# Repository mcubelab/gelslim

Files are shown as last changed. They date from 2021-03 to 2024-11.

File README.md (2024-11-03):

# GelSlim 3.0
**Note:** The MCube Lab at MIT has closed and no longer distributes pre-made sensors by mail upon request.
Consider the latest version [GelSlim 4.0](https://www.mmintlab.com/research/gelslim-4-0/) at the University of Michigan's [MMint Lab](https://www.mmintlab.com/) for an easier to reproduce version of the sensor.

## Quick-Start
Please follow the [Hardware Quick Start Guide](https://github.com/mcubelab/gelslim/blob/main/Hardware/GelSlim%20Quick%20Start%20Tutorial-Updated.pdf) instructions to build your own sensor. The step-by-step resources found below are in the process of being updated.

## Step-by-Step Instructions
**Click on the pictures below for more information**

| 3-D Printing  | PCB Fabrication | Elastomer Fabrication | Assembly |
|---|---|---|---|
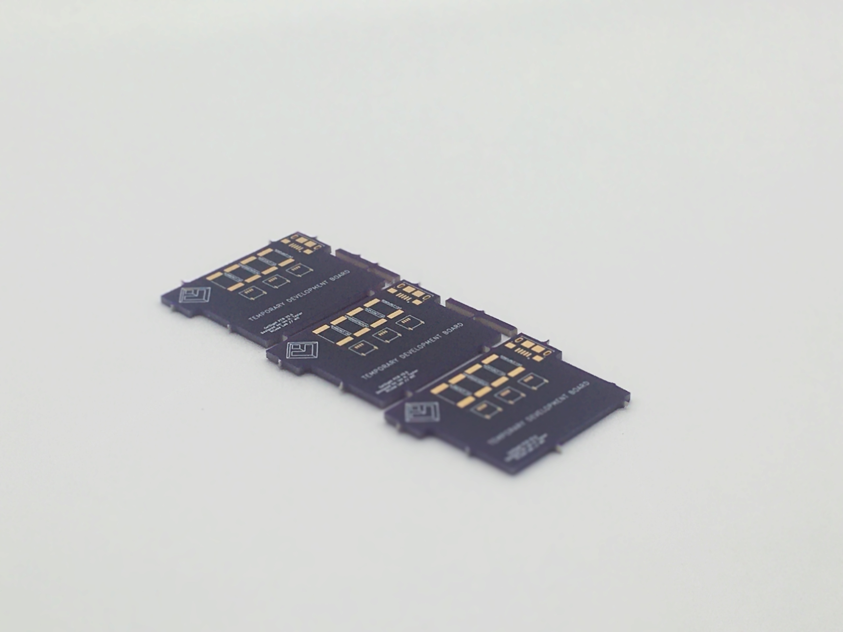
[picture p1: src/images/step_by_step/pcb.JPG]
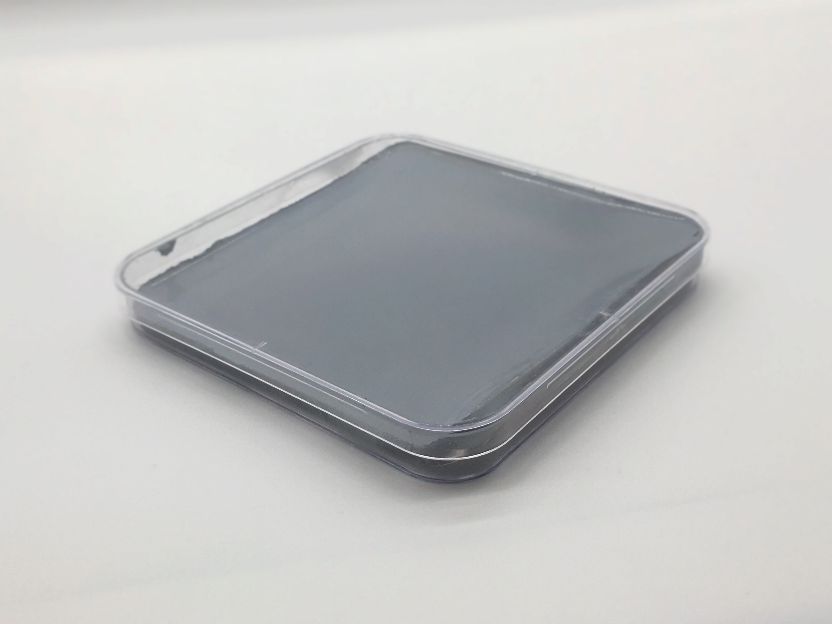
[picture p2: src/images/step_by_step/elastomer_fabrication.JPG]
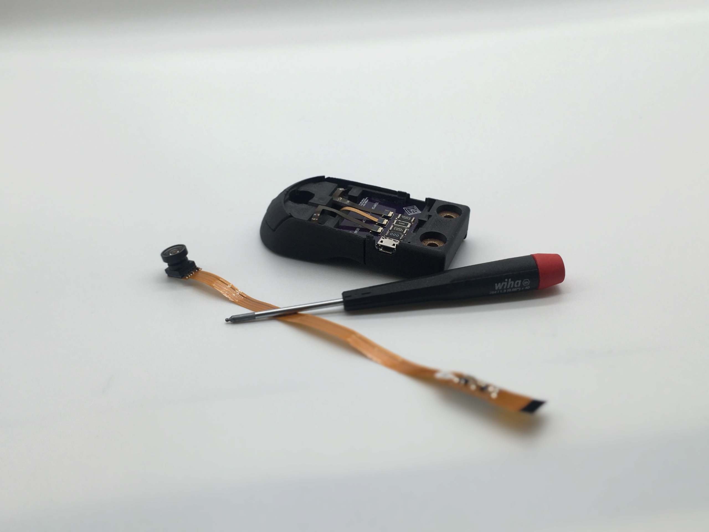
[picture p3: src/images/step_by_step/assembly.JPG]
| | | | | 

## Mechanical
| Elastomer | Fasteners | Body | Shaping Lens |
|---|---|---|---|
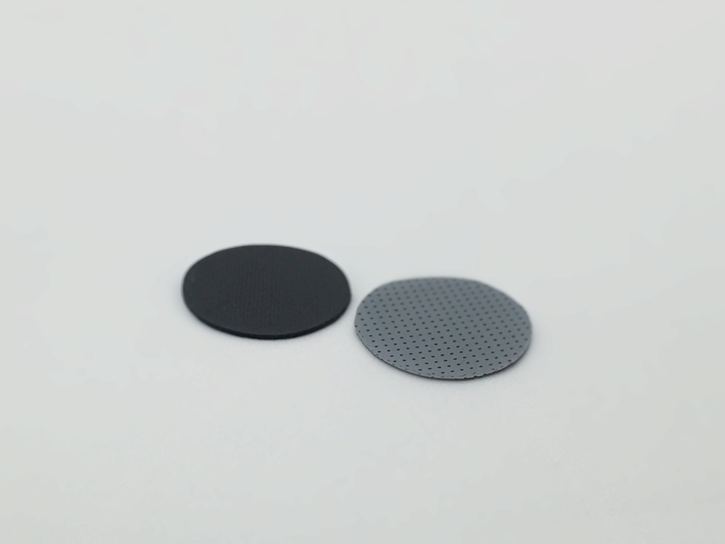
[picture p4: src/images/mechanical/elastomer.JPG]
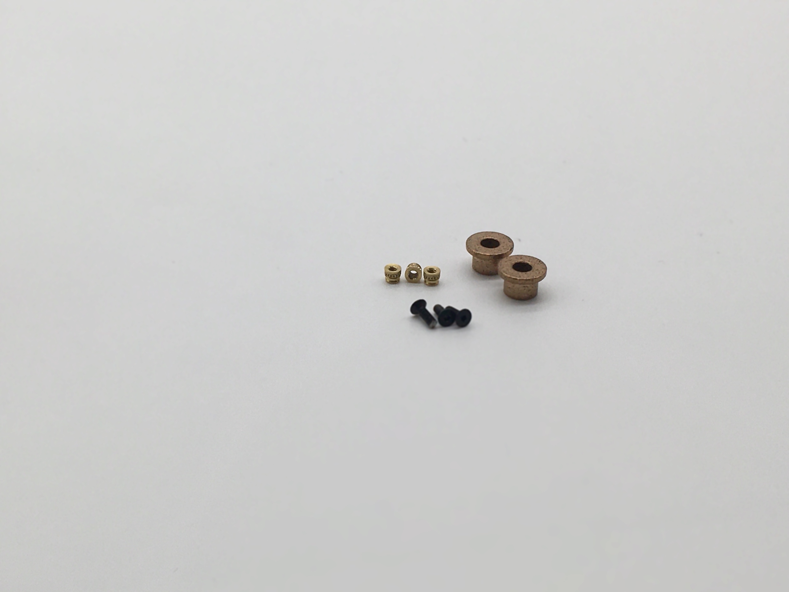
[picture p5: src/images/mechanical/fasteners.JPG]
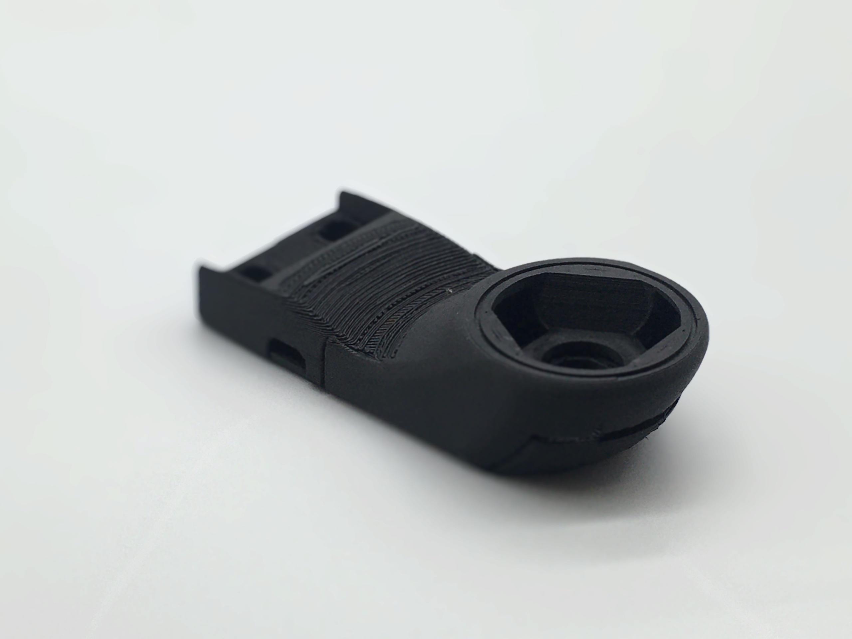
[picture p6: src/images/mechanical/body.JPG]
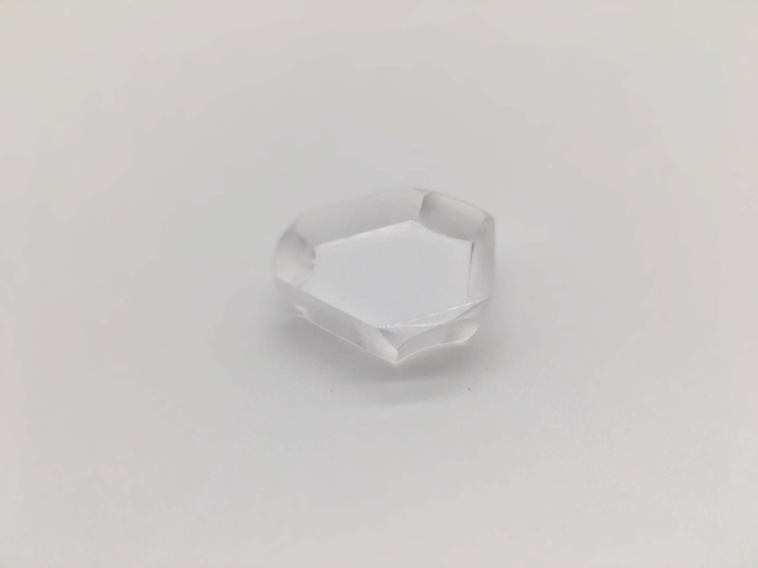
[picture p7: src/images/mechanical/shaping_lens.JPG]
| | | | | 

## Electrical
| LED Driver | LED Harness | Camera | Connectors and Adapters |
|---|---|---|---|
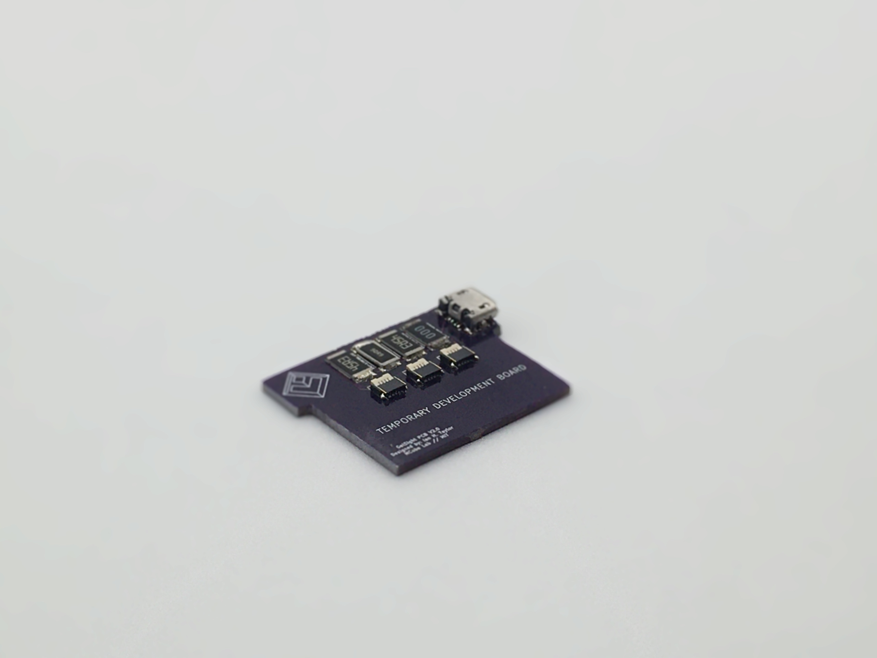
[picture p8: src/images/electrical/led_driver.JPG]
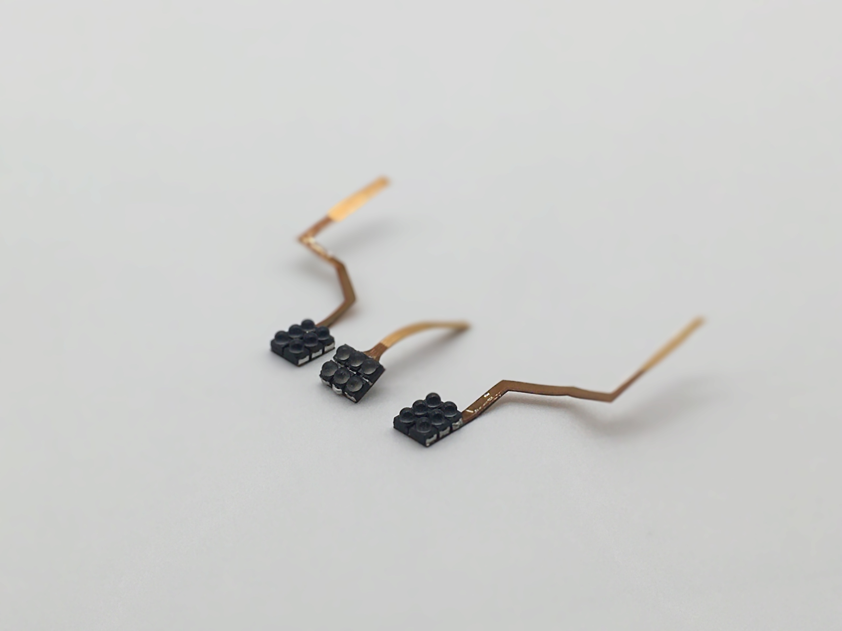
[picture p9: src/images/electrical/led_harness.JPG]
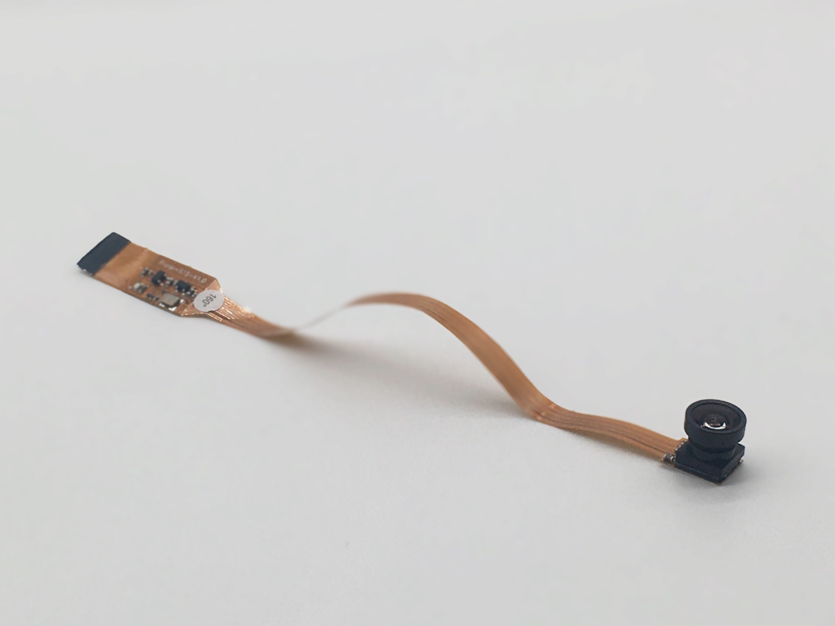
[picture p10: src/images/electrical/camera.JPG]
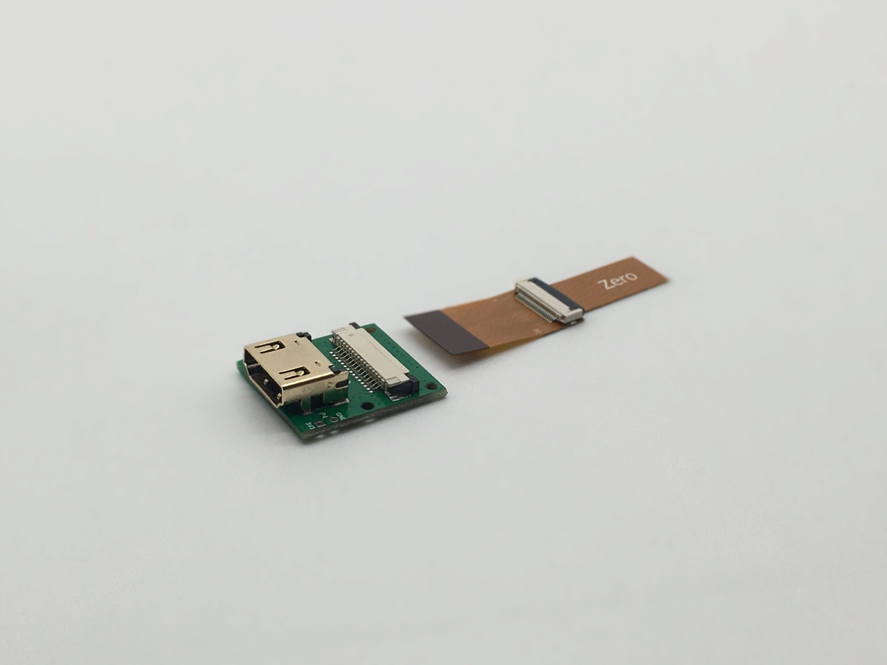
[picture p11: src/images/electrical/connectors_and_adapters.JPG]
| | | | | 

## Software
| Raspberry Pi | Dependencies | GUI | Calibration |
|---|---|---|---|
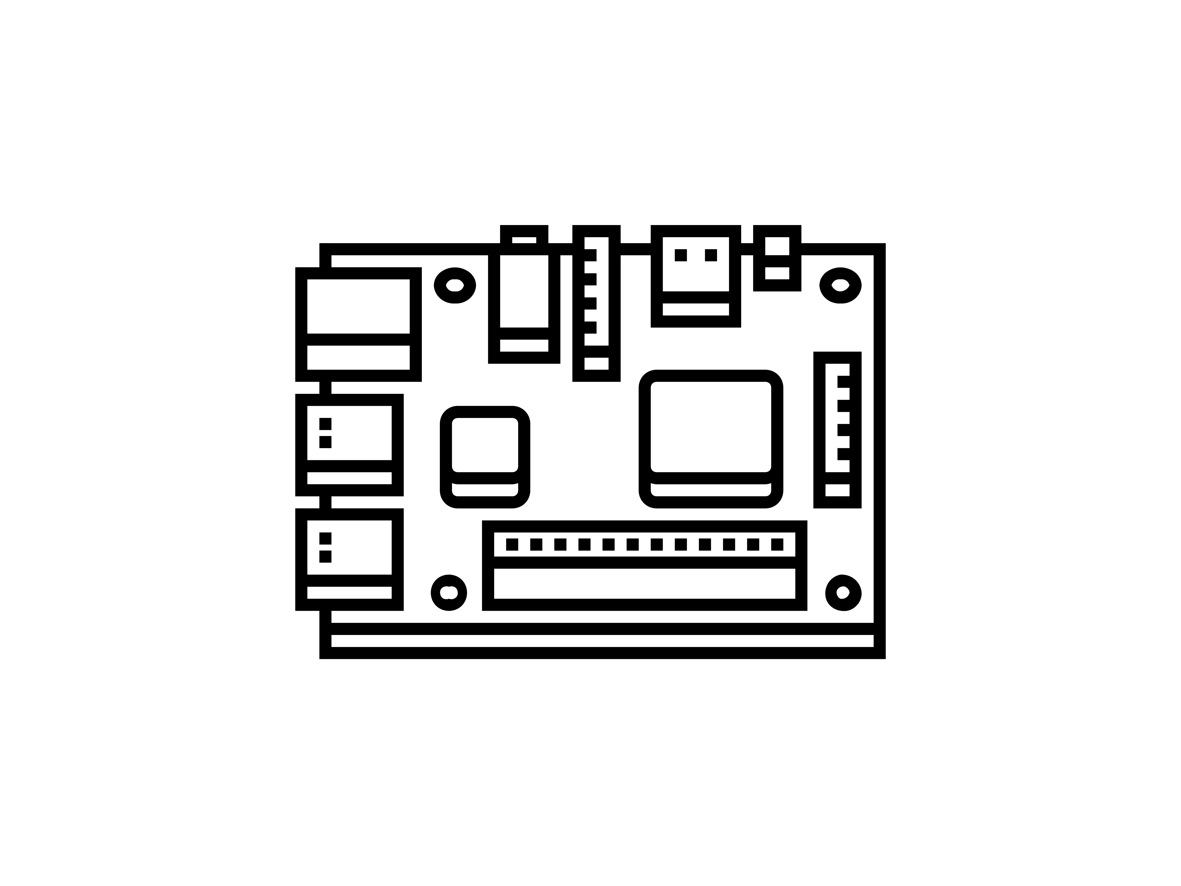
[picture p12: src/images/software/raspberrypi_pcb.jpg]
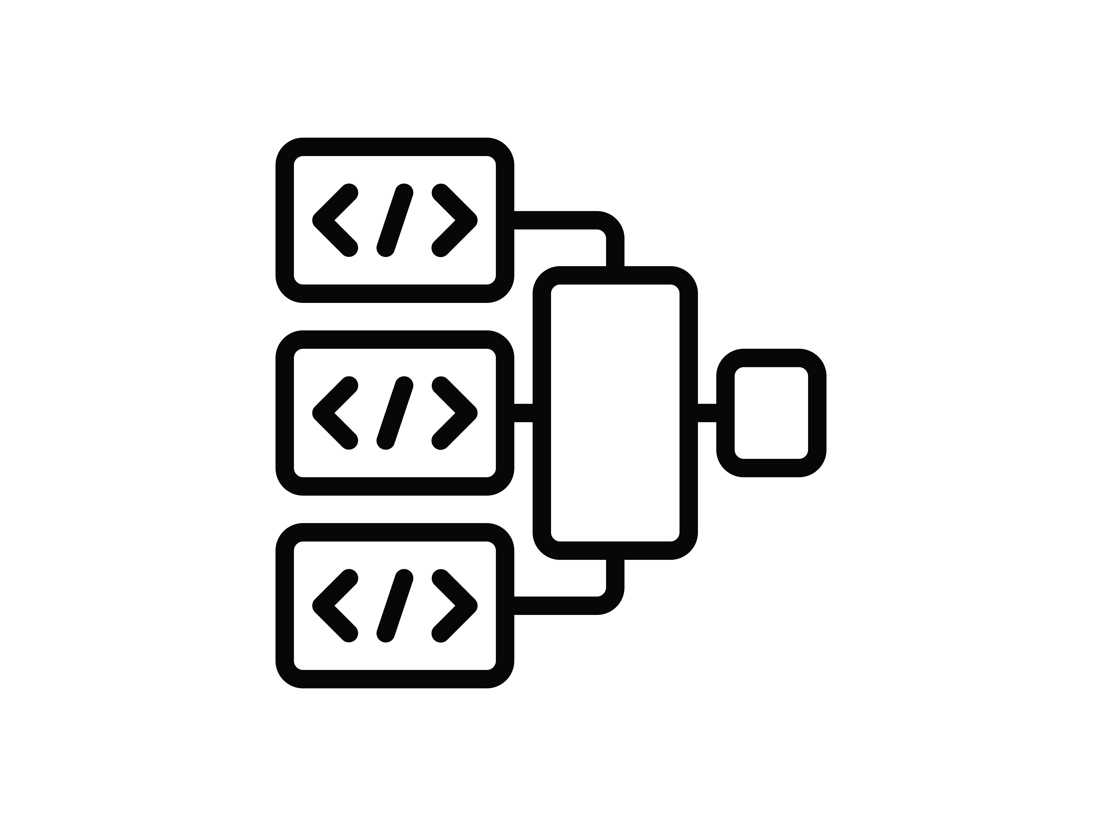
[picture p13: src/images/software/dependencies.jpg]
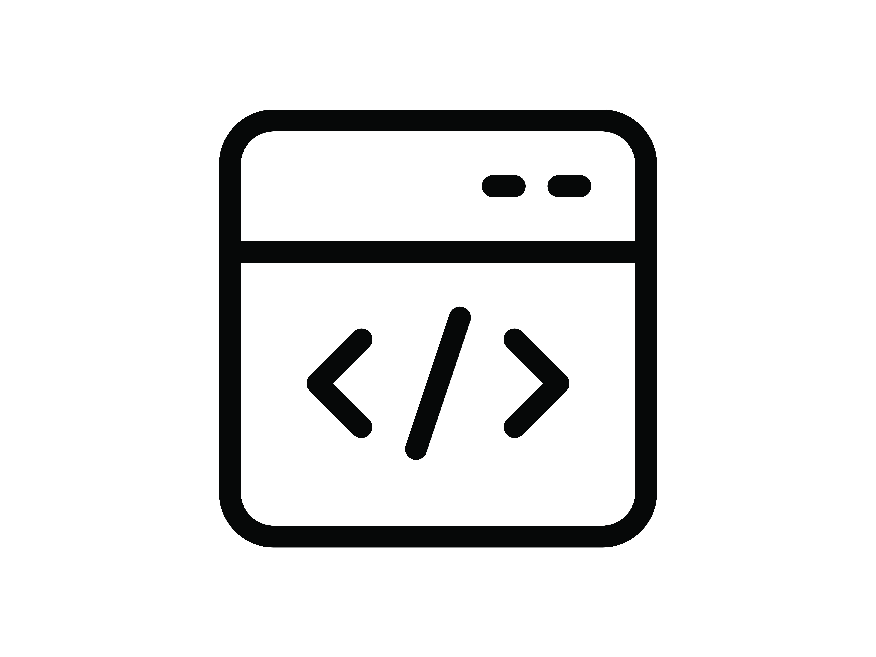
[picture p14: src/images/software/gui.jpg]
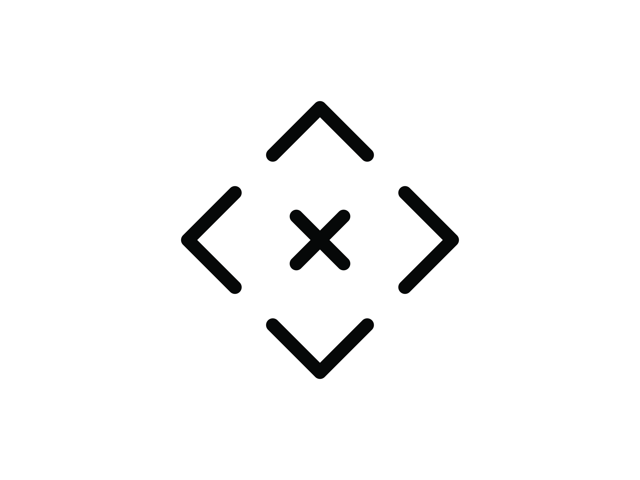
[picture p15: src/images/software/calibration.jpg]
| | | | | 

## More Details
| Mechanical Tools and Consumables | Electronics Components and Tools | Known Issues | Contributing |
|---|---|---|---|
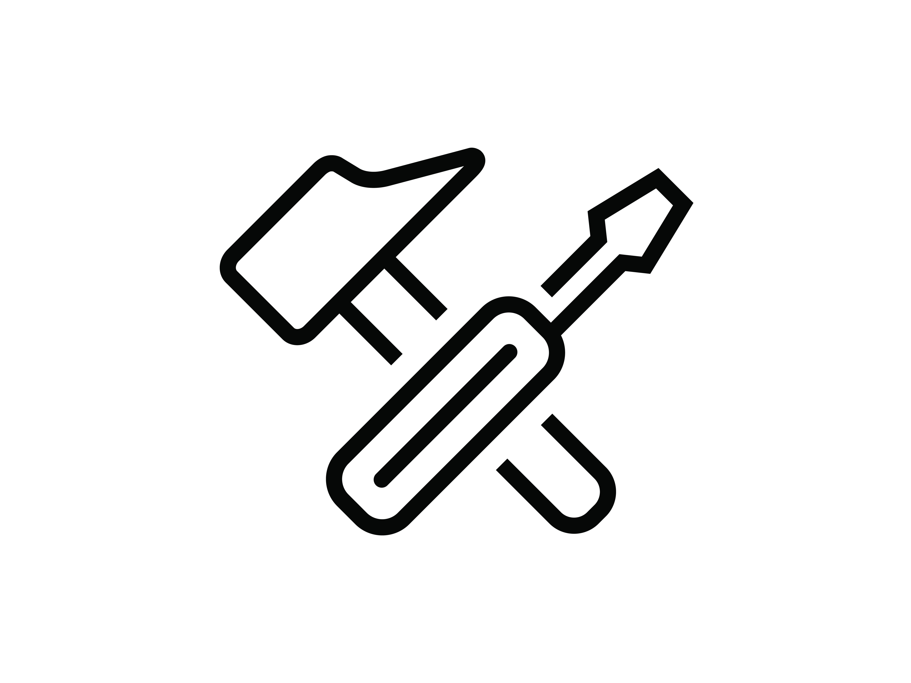
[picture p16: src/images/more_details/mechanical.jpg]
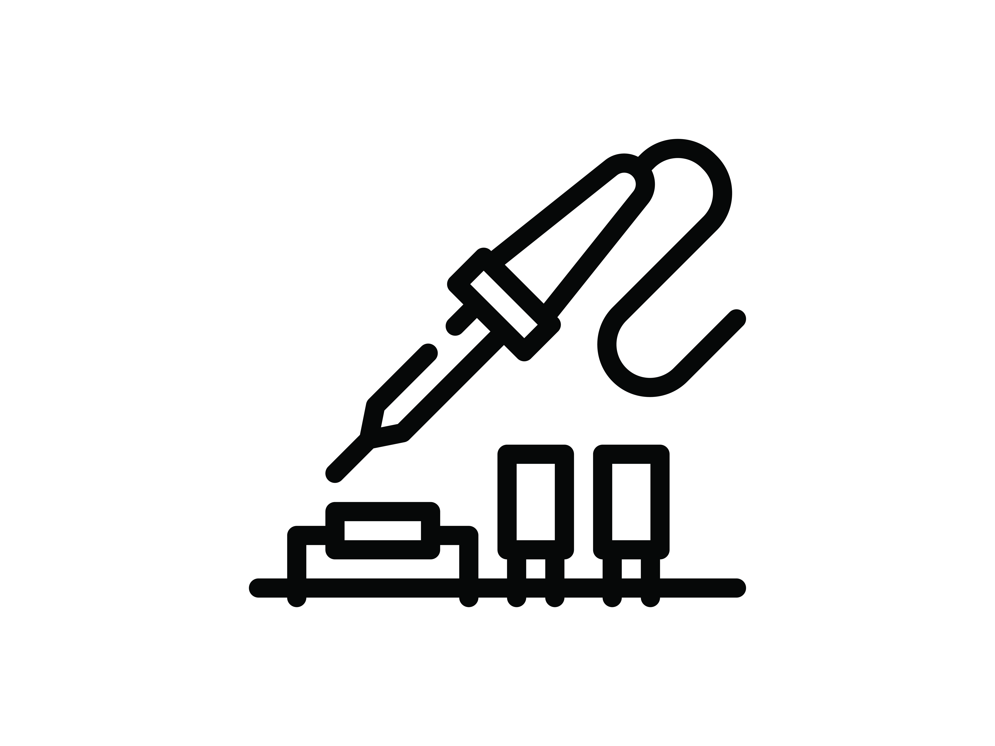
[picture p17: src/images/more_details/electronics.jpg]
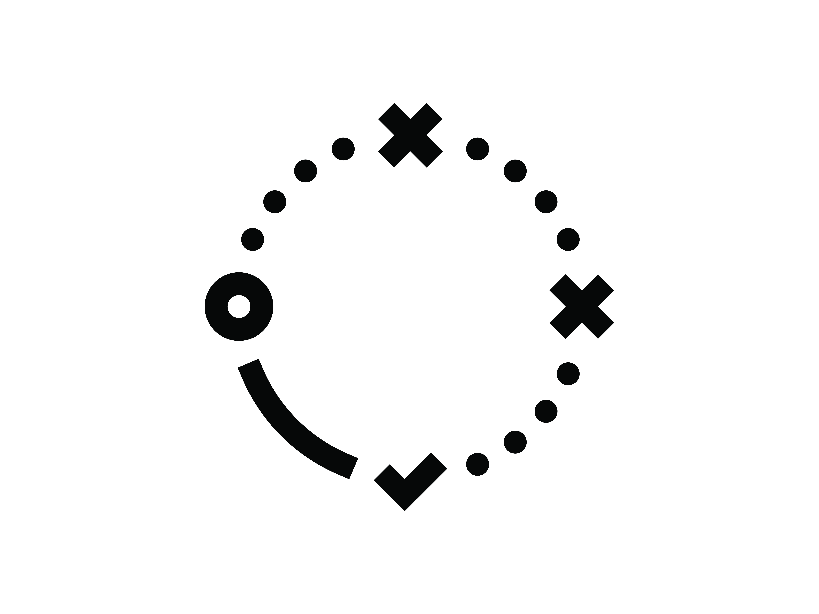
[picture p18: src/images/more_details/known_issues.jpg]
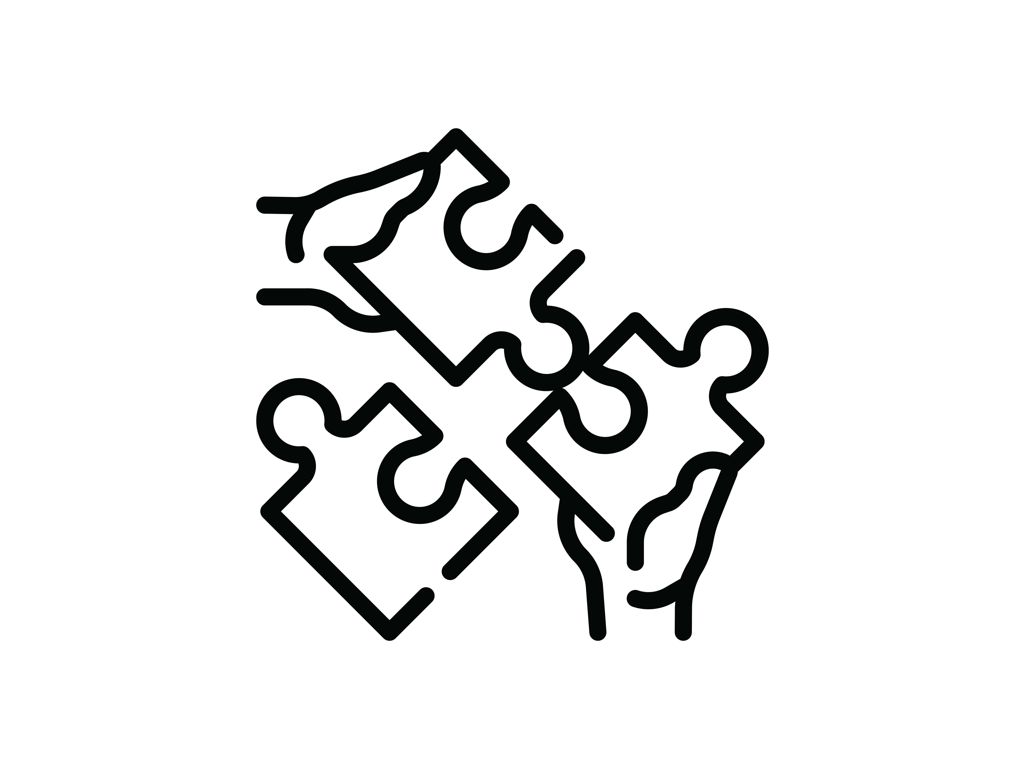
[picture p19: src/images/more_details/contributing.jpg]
| | | | |

## More Information
[GelSlim 3.0 - Webpage](https://ianhtaylor.net/gelslim-30)<br>
[GelSlim 3.0 - Paper](https://arxiv.org/abs/2103.12269)<br>
[GelSlim 3.0 - Demo](https://www.youtube.com/watch?v=Y10XN9byO0g)<br>
[MCube Lab - YouTube Channel](https://www.youtube.com/channel/UCMYUWZTFWZjj7pUc3UPUjig)<br>    

## Notice
This repo is under construction, the following files and folders are not present.
- src/images/step_by_step/3d_printing.jpg
- Image links to and README documentation for root sub-folders
	- Step-by-step Instructions
	- Mechanical
	- Electrical
	- Software
	- More Details
- /Simulation and Optimization/Results
- /Simulation and Optimization/Settings
- /Software/GUI 
  - Tangential Force Calculation
  - Normal Force Calculation

## Authors
Ian Taylor

## License
These design files are licensed under CC-by-NC, as found in the [LICENSE](https://github.com/mcubelab/gelslim/blob/main/LICENSE) file.

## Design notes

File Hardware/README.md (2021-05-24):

# CAD Models
Public model files  of the electrical and mechanical hardware can be found at the following [link](https://cad.onshape.com/documents/d349cbe923c6f7dbdb5a9266/w/20eed945a1a4fb3729cc1f11/e/83841e7147a77c529f63497d)
or can be downloaded individually from the github repo folders.

# Raspicam Spectral Response
Optical transmission information for the Raspicam's OV5647 sensor can be found [here](https://github.com/scivision/raspicam-spectra/).

# LED Datasheets
Datasheets for LED selection can be found on the manufacturers [website](https://www.osram.com/appsn/ProductSelector/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).

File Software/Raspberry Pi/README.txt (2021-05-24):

 RASPBERRY PI - Setup

   1) Purchase a Raspberry Pi 3 with microSD card (>=64gb)
   2) Flash Ubuntu Mate on to the microSD card 
    -https://ubuntu-mate.org/
    -https://www.balena.io/etcher/
   3) Install ROS Melodic on the Raspberry Pi 
    -http://wiki.ros.org/melodic/Installation/Ubuntu
   4) Download the Raspberry Pi Image Files
    -https://drive.google.com/file/d/1tJJFsddHKVC8RBUEtGawACZJs3rvnD6q/view?usp=sharing
   5) Copy the files to the Raspberry Pi and unzip them in the home directory
   6) Follow the instructions in the GUI README to setup video streaming connection with computer over ethernet

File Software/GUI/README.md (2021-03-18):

# GelSlim

## System Requirements
- Ubuntu 18.04 Bionic Beaver
- Python 2.7
- ROS Melodic         
  * *http://wiki.ros.org/melodic/Installation/Ubuntu*
- Python OpenCV 3.4.4 
  * *pip install opencv-python==3.4.4*
- Arp Scan            
  * *sudo apt-get install -y arp-scan*
- NMap
  * *sudo apt-get install nmap*
- Matplotlib          
  * *pip install matplotlib*
- Scipy               
  * *pip install scipy*

## Raspberry Pi Settings
 - Turn on SSH in Ubuntu Mate
   * *sudo systemctl enable ssh*
 
 - Set Raspi IP Manually
   * *IPV4 IP Address: 192.168.1.XXX*
   * *Net Mask: 255.255.255.0*
   * *DNS 8.8.4.4.,8.8.8.8*

## Installation

- Download the GelSlim folder and unzip

- cd to ./GelSlim in terminal

- run python gui.py

## IP Address

### To change the IP Address used for ROS Master and Raspberry Pi use the included arguments for gui.py
#### Note the default IP Addresses are currently set to be "NONE" valued so the script will automatically locate them for you.

  - python gui.py -a 1      *Finds IP Addresses automatically using **arp** terminal command*

  - python gui.py -a 2      *Set IP Addresses manually*
  
  - change the default IP Address in line 21-22 of gui.py
  
  - **NOTE:** the local name and password for the raspberry pi must be "raspi" for the automatic login of ssh to work
              if this is not the case you must change the local name and password within "raspberry_new.launch"
    
## Error Log

https://docs.google.com/document/d/1r3EBdHhFpfCTQFS_eKzmCBGyteXqJAIMatUEwNnOWO8/edit

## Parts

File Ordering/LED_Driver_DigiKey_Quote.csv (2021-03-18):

Digi-Key Part Number | Manufacturer | Manufacturer Part Number | Description | Customer Reference | Quantity 1 | Price | Quantity 2 | Price | Quantity 3 | Price | Stock Status | Mfg Std Lead Time | Comments | RoHS Status | Lead Free Status | REACH Status
541-0.0XCT-ND | VISHAY DALE (VA) | CRCW25120000Z0EG | RES SMD 0 OHM JUMPER 1W 2512 |  | 1 | 0.28000 | 10 | 0.23400 | 100 | 0.09100 | IN STOCK | 28 Weeks | Alternate Packaging Exists | ROHS3 Compliant | Lead free | Not Available
609-4616-1-ND | AMPHENOL FCI (VA) | 10118193-0001LF | CONN RCPT USB2.0 MICRO B SMD R/A |  | 1 | 0.41000 | 10 | 0.38800 | 100 | 0.27100 | IN STOCK | 14 Weeks | Alternate Packaging Exists Import Tariff may apply to this part if shipping to the United States | RoHS Compliant | Lead free | Unaffected Jan-2021
255-5484-1-ND | PANASONIC ELECTRIC WORKS (VA) | AYF530265T | CONN FPC 2POS 0.50MM R/A |  | 3 | 1.52000 | 30 | 1.29000 | 300 | 1.06600 | IN STOCK | 10 Weeks | Alternate Packaging Exists | RoHS Compliant | Lead free | Not Available
YAG5595CT-ND | YAGEO (VA) | AC2512FK-0745R3L | RES SMD 45.3 OHM 1% 1W 2512 |  | 2 | 0.46000 | 20 | 0.34400 | 200 | 0.14500 | IN STOCK | 20 Weeks | Alternate Packaging Exists Import Tariff may apply to this part if shipping to the United States | ROHS3 Compliant | Lead free | Unaffected Jun-2020
RMCF2512FT60R4CT-ND | STACKPOLE ELECTRONICS INC (VA) | RMCF2512FT60R4 | RES 60.4 OHM 1% 1W 2512 |  | 1 | 0.32000 | 10 | 0.26900 | 100 | 0.10500 | IN STOCK | 21 Weeks | Alternate Packaging Exists | ROHS3 Compliant | Lead free | Unaffected Jun-2020

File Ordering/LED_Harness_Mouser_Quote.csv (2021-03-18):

SHOPPING CART
This is not an invoice
18-Mar-21 11:27:07
 | Mouser # | Mfr. # | Manufacturer | Customer # | Description | RoHS | Lifecycle | Order Qty. | Price (USD) | Ext.: (USD)
1 | 720-LBT66GV2CAA7291 | LB T66G-V2CA-59-Z484 | Osram Opto Semiconductor |  | Standard LEDs - SMD Blue TOPLED TF | RoHS Compliant | Obsolete | 100 | $-.-- | $-.--
2 | 720-LTT66GCBEAA7293 | LT T66G-CBEA-29-N424-20-R33-Z | Osram Opto Semiconductor |  | Standard LEDs - SMD True Green TOPLED Black | RoHS Compliant | New Product | 100 | $0.324 | $32.40
3 | 720-LRT66FAABB11Z | LR T66F-AABB-1-1-Z | Osram Opto Semiconductor |  | Standard LEDs - SMD Red | RoHS Compliant |  | 100 | $0.242 | $24.20
By submitting your order you agree to these terms and conditions. |  |  |  |  |  |  |  |  | Merchandise: | $56.60
Prices are reflected at the date and time shown. |  |  |  |  |  |  |  |  | Shipping Charge: | $7.99

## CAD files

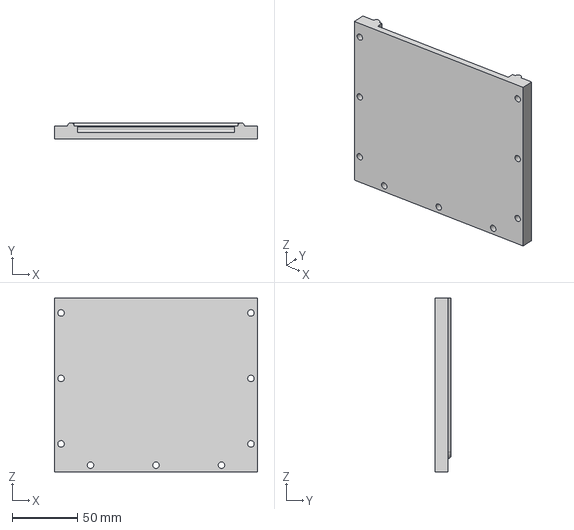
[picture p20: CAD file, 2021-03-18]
Hardware/Mechanical/Elastomer/mold_front.step
155.0 x 12.5 x 132.5 mm

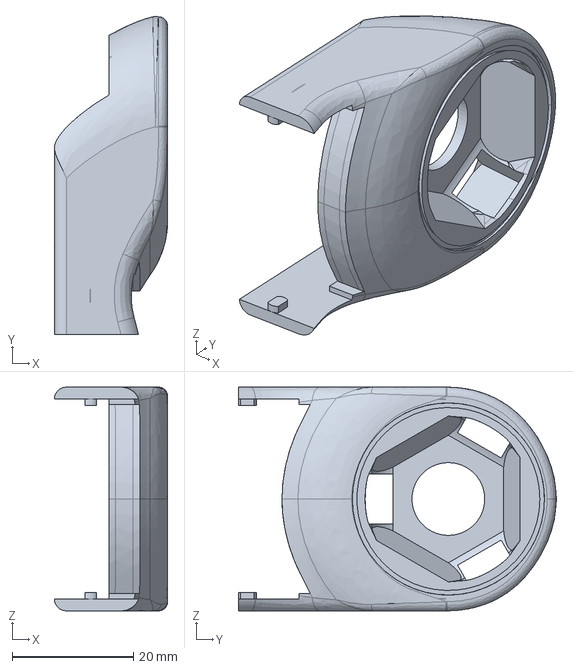
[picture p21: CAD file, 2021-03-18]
Hardware/Mechanical/Finger/Robtiq 2F-85/STEP/finger_tip.step
18.7 x 52.5 x 36.9 mm

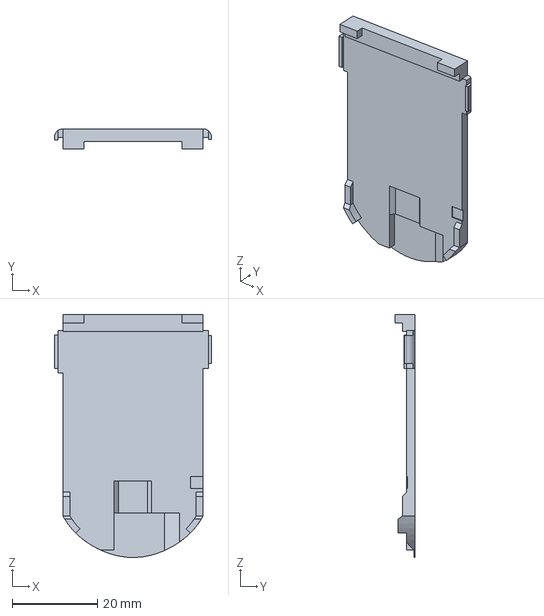
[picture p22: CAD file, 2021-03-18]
Hardware/Mechanical/Finger/Weiss WSG-32/STEP/finger_back.step
36.9 x 4.80 x 57.1 mm

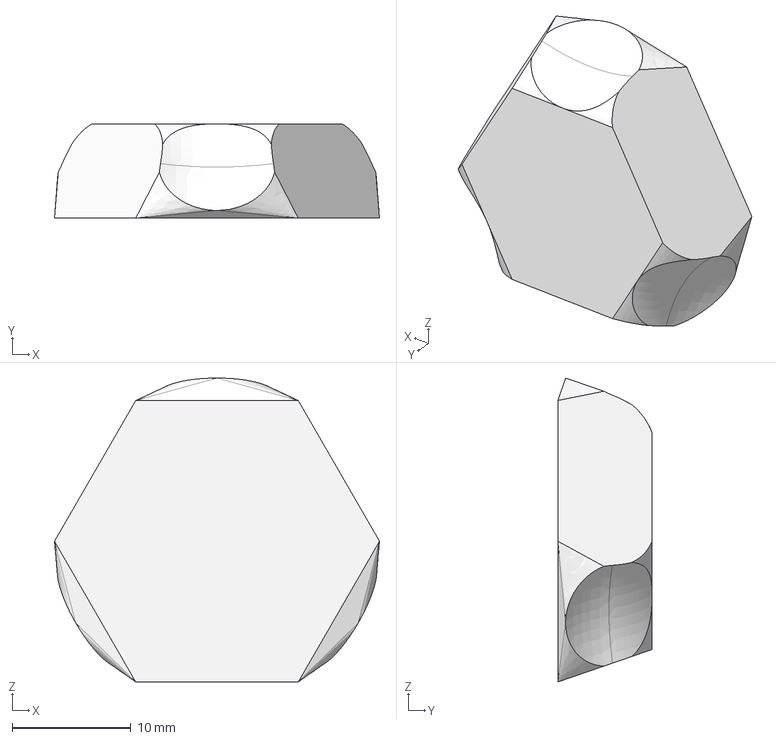
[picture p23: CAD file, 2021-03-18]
Hardware/Mechanical/Shaping Lens/shaping_lens.step
27.4 x 7.94 x 25.6 mm

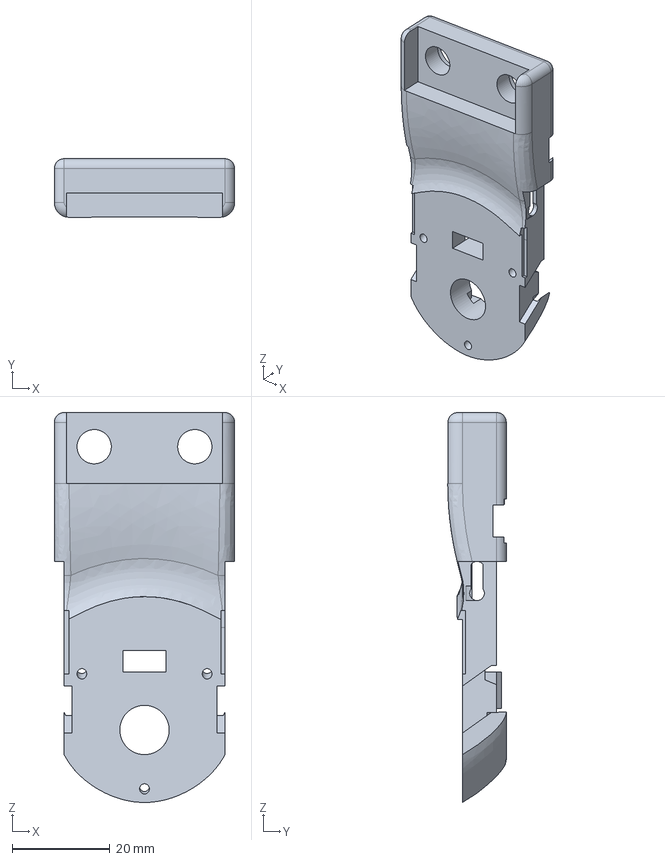
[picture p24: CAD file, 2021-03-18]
Hardware/Mechanical/Finger/Weiss WSG-32/STEP/finger_body.step
36.9 x 12.0 x 79.9 mm

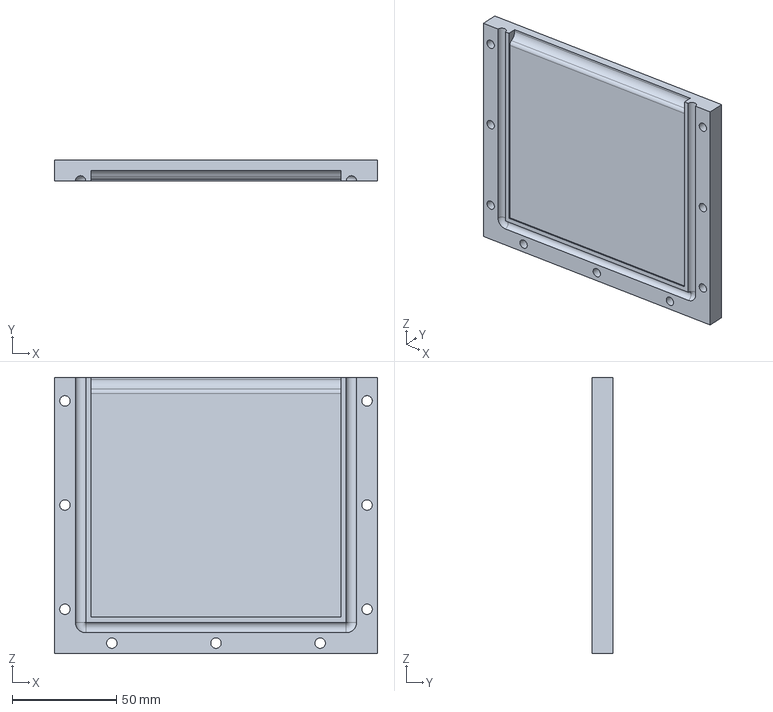
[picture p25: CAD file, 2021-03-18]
Hardware/Mechanical/Elastomer/mold_back.step
155.0 x 10.0 x 132.5 mm

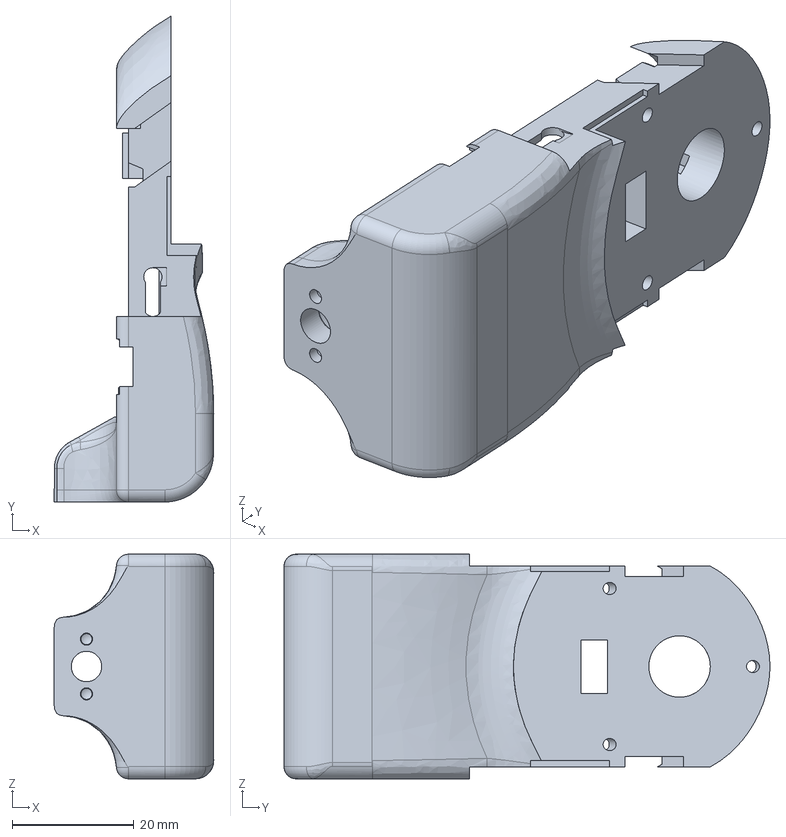
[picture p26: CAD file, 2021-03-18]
Hardware/Mechanical/Finger/Robtiq 2F-85/STEP/finger_body.step
26.2 x 79.9 x 36.9 mm

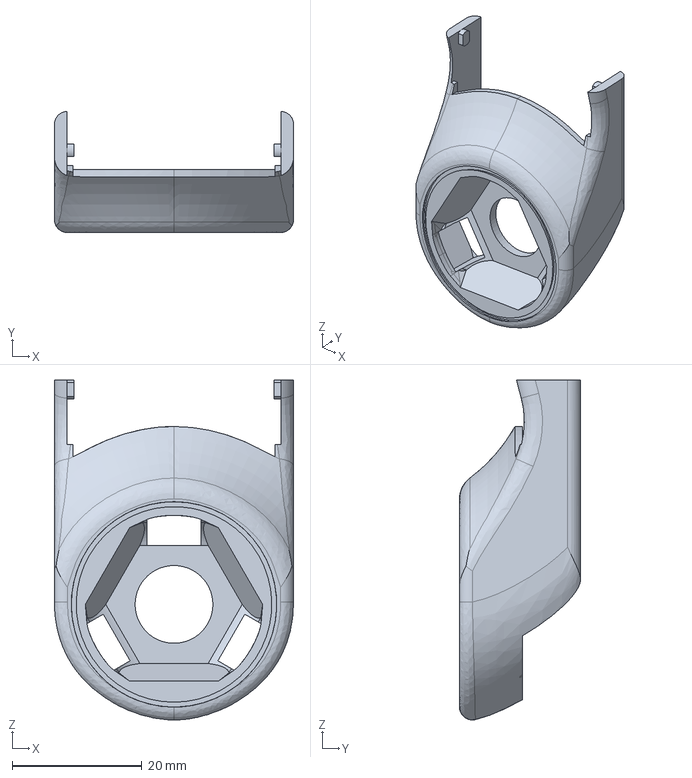
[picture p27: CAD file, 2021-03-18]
Hardware/Mechanical/Finger/Weiss WSG-32/STEP/finger_tip.step
36.9 x 18.7 x 52.5 mm

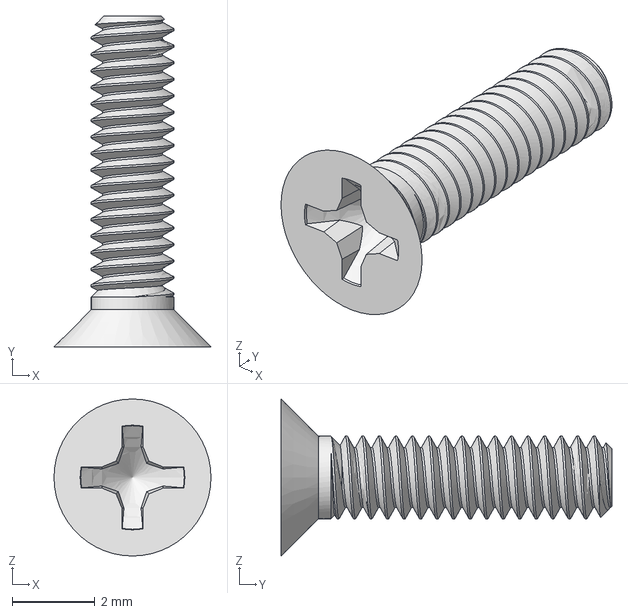
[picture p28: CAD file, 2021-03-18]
Hardware/Mechanical/Fasteners/91698A204_METRIC 18-8 SS FLAT HEAD PHIL MACHINE SCREW.step
3.80 x 8.00 x 3.80 mm

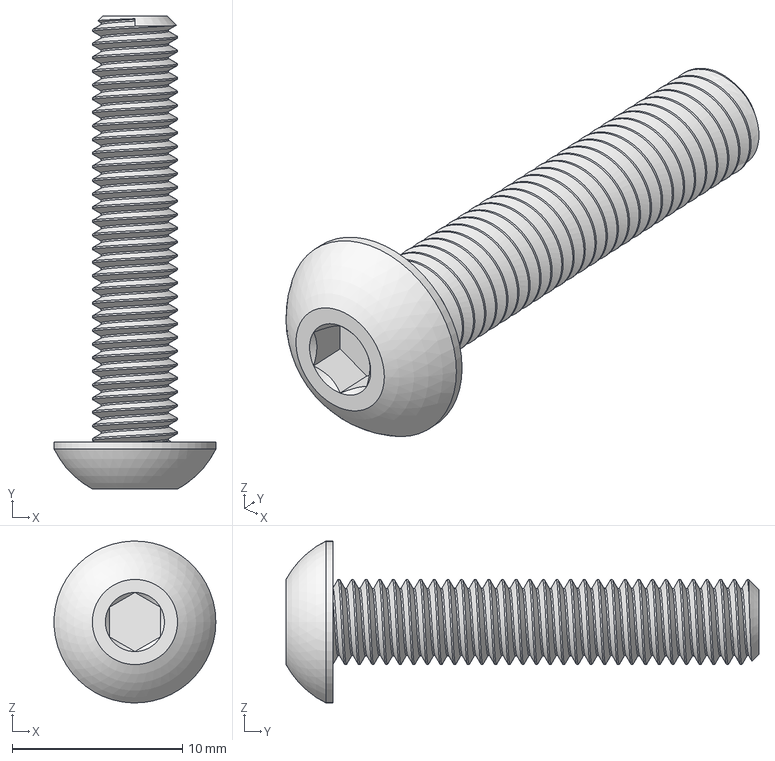
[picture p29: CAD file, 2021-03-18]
Hardware/Mechanical/Elastomer/92095A216_BUTTON HEAD HEX DRIVE SCREW.step
9.49 x 27.8 x 9.50 mm

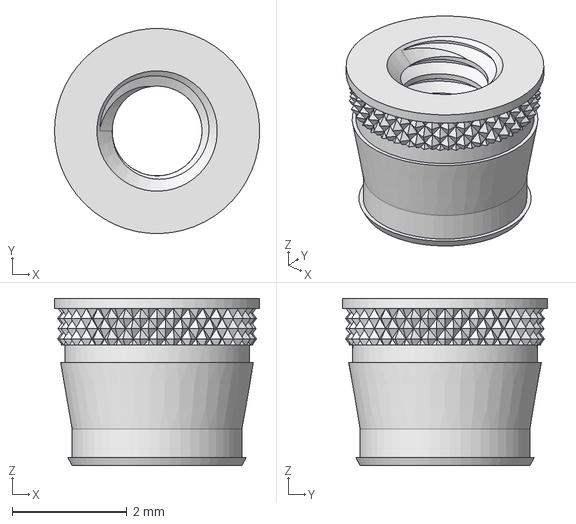
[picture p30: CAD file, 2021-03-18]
Hardware/Mechanical/Fasteners/94180A307_HEAT-SET INSERTS FOR PLASTICS.step
3.58 x 3.58 x 2.92 mm

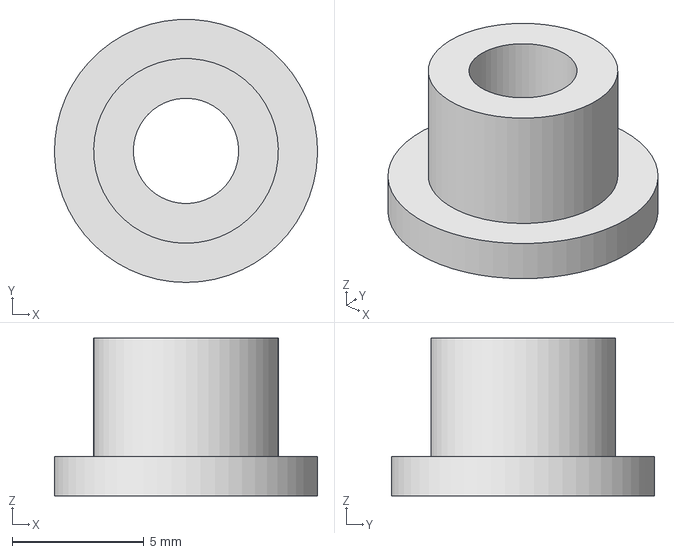
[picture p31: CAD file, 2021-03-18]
Hardware/Mechanical/Fasteners/6659K650_OIL-EMBEDDED FLANGED SLEEVE BEARING.step
10.00 x 9.99 x 6.00 mm

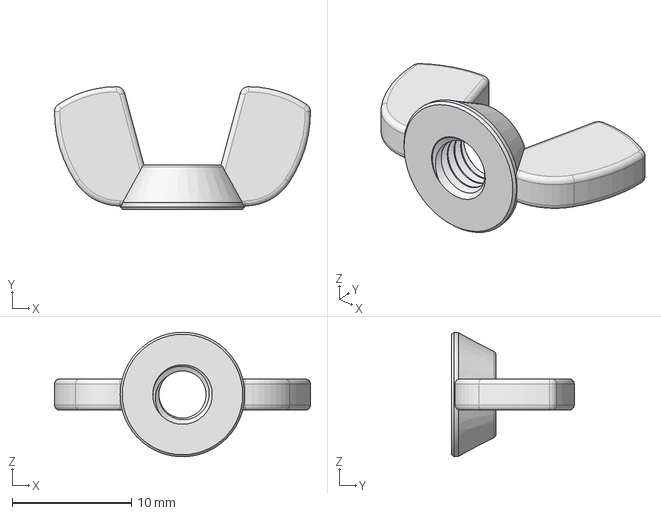
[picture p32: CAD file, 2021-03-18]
Hardware/Mechanical/Elastomer/94545A225_18-8 SS WING NUTS.step
21.5 x 10.3 x 10.5 mm

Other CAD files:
Hardware/Mechanical/Finger/Robtiq 2F-85/STEP/finger_back.step
Hardware/Mechanical/Finger/Robtiq 2F-85/STL/finger_back.stl
Hardware/Mechanical/Finger/Robtiq 2F-85/STL/finger_body.stl
Hardware/Mechanical/Finger/Robtiq 2F-85/STL/finger_tip.stl
Hardware/Mechanical/Finger/Weiss WSG-32/STL/finger_back.stl
Hardware/Mechanical/Finger/Weiss WSG-32/STL/finger_body.stl
Hardware/Mechanical/Finger/Weiss WSG-32/STL/finger_tip.stl

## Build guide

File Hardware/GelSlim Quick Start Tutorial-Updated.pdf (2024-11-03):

# GelSlim 3.0 Hardware Quick Start Tutorial

# MCube Manipulations and Mechanisms Lab

# Foreword

GelSlim 3.0 is a tactile-sensing finger used for the high-resolution measurement of shape, force and slip. We are open sourcing this project to stimulate future research in tactile-sensing and provide the robotics community access to reliable and easily-reproducible tactile finger with a diversity of sensing modalities. NOTICE: The MCube Manipulations and Mechanisms Lab NO LONGER distributes pre-made

sensors by mail upon request.

Please see the latest version of Gelslim, GelSlim 4.0 (https://www.mmintlab.com/research/gelslim-4-0/) courtesy of Sipos et. al. (https://arxiv.org/pdf/2409.19770) (@University of Michigans MMint Lab) for an easily reproducible iteration of the sensor.

# Step 1. Component Ordering

Purchase the following off-the-shelf components at the given links.

Component | Quantity
Odseven 160° Variable Focus Raspicam (https://odseven.com/collections/raspberry-pi-camera/products/odseven-camera-for-raspberry-pi-zero-160-lens-15cm-long-5mp) | 2
Odseven Camera Cable Adapter (https://odseven.com/collections/raspberry-pi-camera/products/odseven-camera-cable-adapter) | 2
Raspberry Pi 3B Kit (https://www.amazon.com/CanaKit-Raspberry-Premium-Clear-Supply/dp/B07BC7BMHY) | 2
MicroSD Card and Adapter (https://www.amazon.com/SanDisk-microSDHC-Standard-Packaging-SDSQUNC-032G-GN6MA/dp/B010Q57T02) | 2
HDMI Cable (https://www.amazon.com/AmazonBasics-High-Speed-HDMI-Cable-3-Pack/dp/B014I8SX4Y) | 1
CSI to HDMI Adapter (https://www.amazon.com/Arducam-Extension-Module-Raspberry-Specific/dp/B06XDNBM63) | 2
Left-Angle Micro USB Cable (https://www.amazon.com/gp/product/B08D77LYHT/ref=ppx_yo_dt_b_asin_title_o01_s00?ie=UTF8&psc=1) | 2

Step 1. Component Ordering Cont.

Purchase the following off-the-shelf components at the given links.

Component | Quantity
McMaster Carr - Oil Bearing (https://www.mcmaster.com/6659K65/) | 4
McMaster Carr - M2 Screws (Pack of 100) (https://www.mcmaster.com/91698A204/) | 1
McMaster Carr - M2 Heat Inserts (Pack of 100) (https://www.mcmaster.com/94180A307/) | 1
XP-565 Silicone (http://www.silicones-inc.com/index.php/about/product-datasheets/addition-cure-silicone-products-data-sheets/) | 1
Black Print-On Silicone Ink (https://www.rawmaterialsuppliers.com/product/black-silicone-ink/) | 1
Gray Print-On Silicone Ink (https://www.rawmaterialsuppliers.com/product/gray-silicone-ink/) | 1
NOVOCS Gloss Silicone Solvent (https://www.reynoldsam.com/product/novocs/) | 1
Gorilla Glue Clear Silicone Sealant (https://www.amazon.com/Gorilla-Percent-Silicone-Sealant-Squeeze/dp/B01B5RBOA6) | 1
Sakura Pigma Black Ink Pen (https://www.amazon.com/Sakura-Pigma-Graphic-Pen-PACK/dp/B00DUGYCIC) or Faber Castell Black Ink Pen (https://www.amazon.com/Faber-Castell-Artist-Pen-Black-1-5mm-Bullet/dp/B01E46ZX66) | 1

# Step 2. Finger Fabrication

## 3D print the finger body, back, and tip. Orient the parts on the print-bed according to the diagram below. Use 0.1 mm layer height, supports, and 30-100%

Infill (dependent on the application requirements of the application).
Recommended 100% Infill for maximum stiffness.

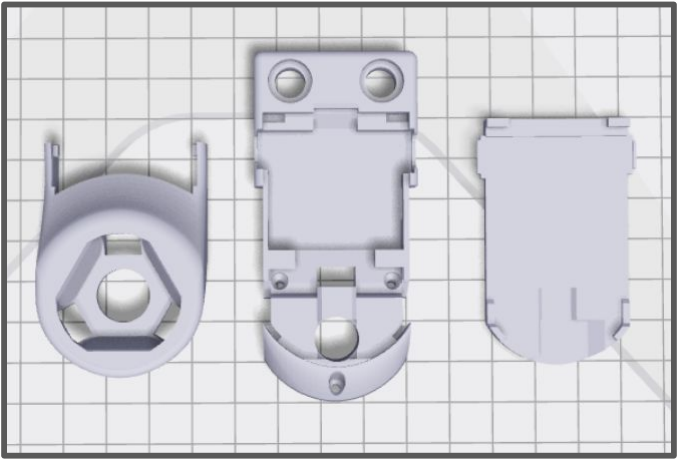
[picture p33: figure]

# Step 3. Gel Mold Fabrication

Order the acrylic mold from a turnkey fabrication service (we utilize SuNPe Inc.). (https://www.sunpe.com/)

## Request polishing to a translucent finish on the inner faces of each of the mold halves as shown in the diagram below (LEFT). Assemble the mold according to

the diagram shown below (RIGHT).

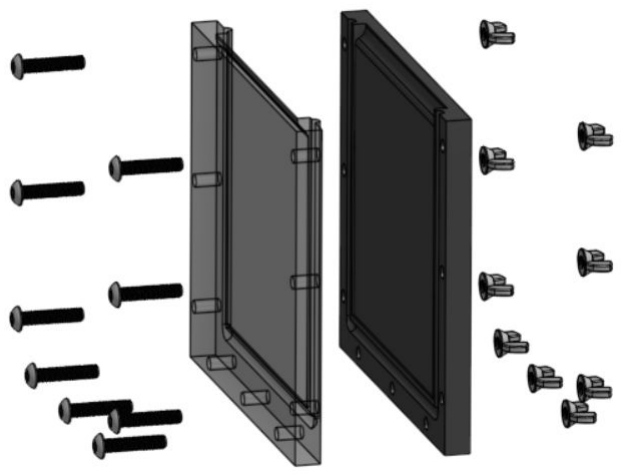
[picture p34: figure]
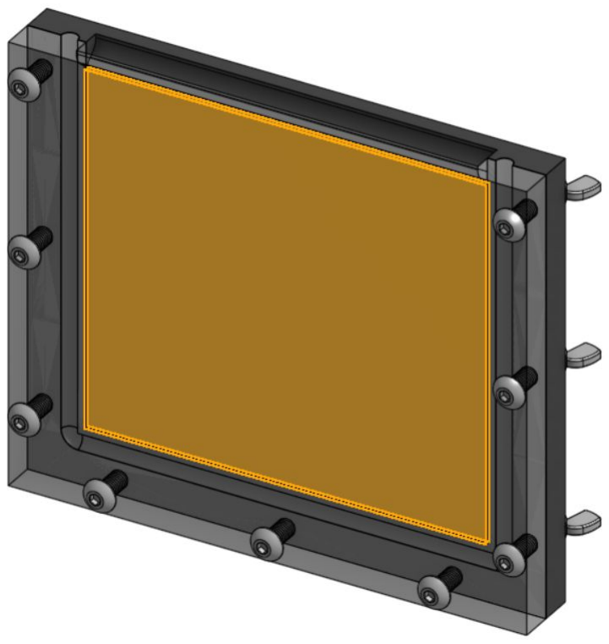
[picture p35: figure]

# Step 4. Gel Fabrication

Take proper precautions when fabricating the elastomer gel. Use of the following PPE is required during fabrication: Nitrile Gloves, Respirator, Safety Glasses. Perform all spraying and painting within an adequately ventilated spray-booth/fume-hood.

1. Mix the XP565 (Silicones Inc.) platinum-based silicone in a 1:10 ratio of activator to base.
2. Degas in a vacuum chamber.
3. Pour into the acrylic mold and leave to cure for 24 hours.
4. Mix the reflective layer using a Gray Print-On Silicone Ink using a 10:1 ratio of silicone ink to its catalyst.
5. Add a NOVOCS Gloss Silicone Solvent to dilute the silicone ink in a 1:10:30 ratio of ink catalyst to ink to solvent.
6. Airbrush the reflective layer on top of the elastomer until the surface is no longer translucent.
7. Let the reflective layer cure for 24 hours.
8. Laser cut holes in a grid pattern on the painted surface of the elastomer and adding Black Print-On Silicone Ink.
9. Seal the marker layer was sealed by spraying an additional layer of black silicone ink using the previous 1:10:30 ratio of ink catalyst to ink to solvent.
10. Let the marker grid cure for 24 hours.
11. Cut the gel to shape using the cutting template.

# Step 5. PCB Ordering and Fabrication

Order the PCBs from one of the following turnkey fabrication services. The capabilities of each service is listed.

*DIY surface mount soldering tools are listed in the following section.

Service | PCB Fabrication | PCB Assembly
Advanced Circuits (https://www.4pcb.com/) | ✔ | ✔
PCBWay (https://www.pcbway.com/) | ✔ | ✔
OSHPARK* (https://oshpark.com/) | ✔ | ✘

# Step 6. PCB Fabrication

Component | Quantity
X-Acto Precision Knife (https://www.amazon.com/X-Acto-XZ3601-X-ACTO-Knife-Safety/dp/B005KRSWM6) | 1
Lead Free Solder-Paste (https://www.amazon.com/Clean-Temperature-Solder-Paste-Grams/dp/B017RSGPI8?cv_ct_cx=solder+paste) | 1
SMT Solder Plate (https://www.amazon.com/Remover-Heating-Soldering-Welding-Station/dp/B07W1ZZH8T?s=hi) | 1
Precision Tweezer Set (https://www.amazon.com/Precision-Stainless-Electronic-Anti-static-Industrial/dp/B08DN6MYTP?s=hi) | 1

# Step 7. Shaping Lens Fabrication

Order the acrylic lens from a turnkey fabrication service (we utilize SuNPe Inc.). (https://www.sunpe.com/)

## Request polishing to a translucent finish on the top and bottom faces as shown in the diagram below (LEFT). Paint the flat faces opposing the acrylic lens's shaping

geometry with a black ink pen as shown in the diagram below (RIGHT).

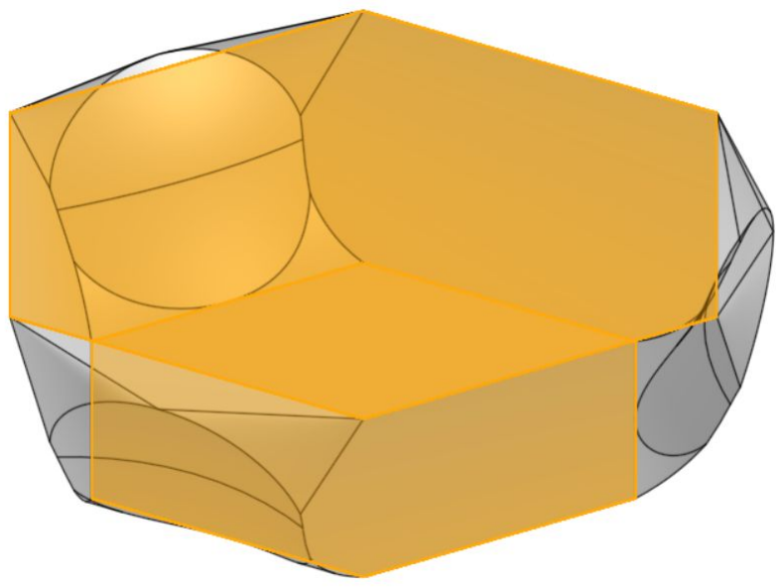
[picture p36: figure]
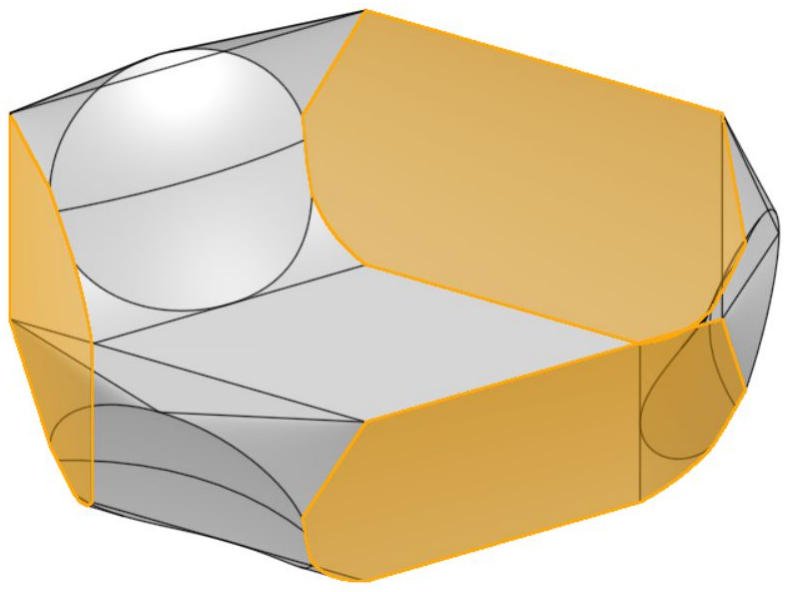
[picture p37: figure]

# Step 8. Assembly

1. Use a soldering iron to place the M2 Heat Inserts in the Finger-Tip.
2. Press-fit the following components into place according to the diagram below. Note: fold the camera module cable to exit the routing hole prior to press fitting the finger back into position.
3. Bond the gel to the acrylic lens and finger-body using Gorilla Silicone Clear Sealant.

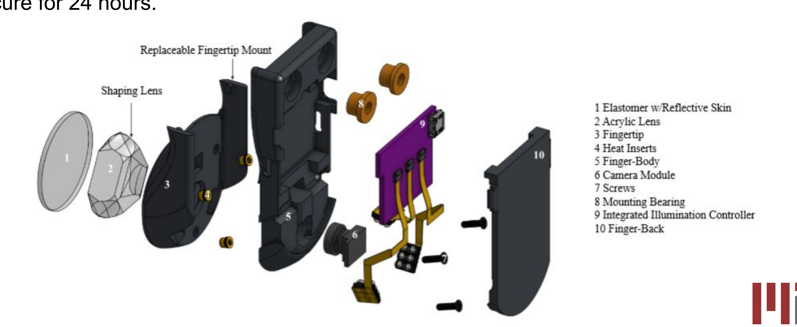
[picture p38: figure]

4. Leave to cure for 24 hours.

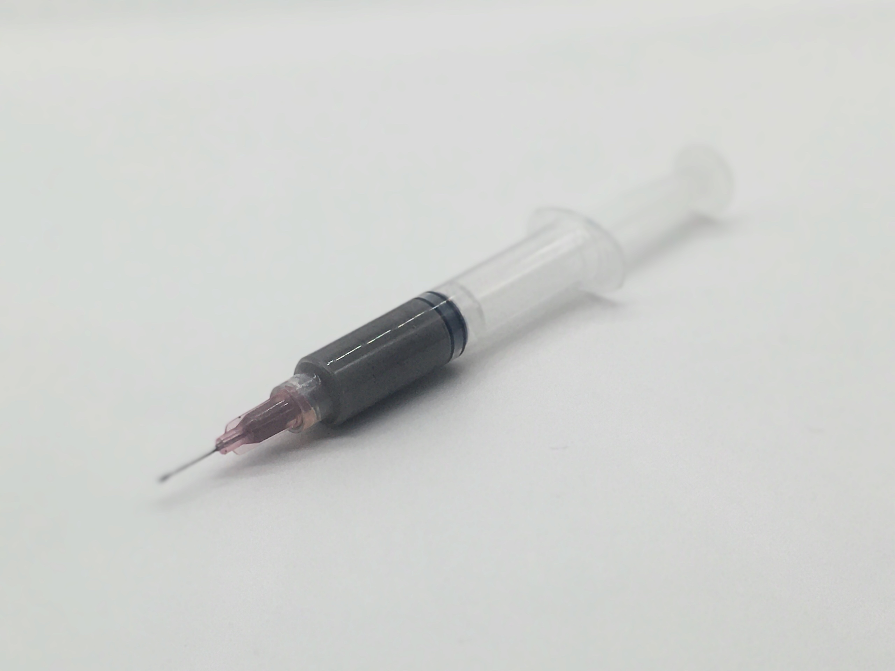
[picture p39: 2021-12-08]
src/images/solder_paste.JPG

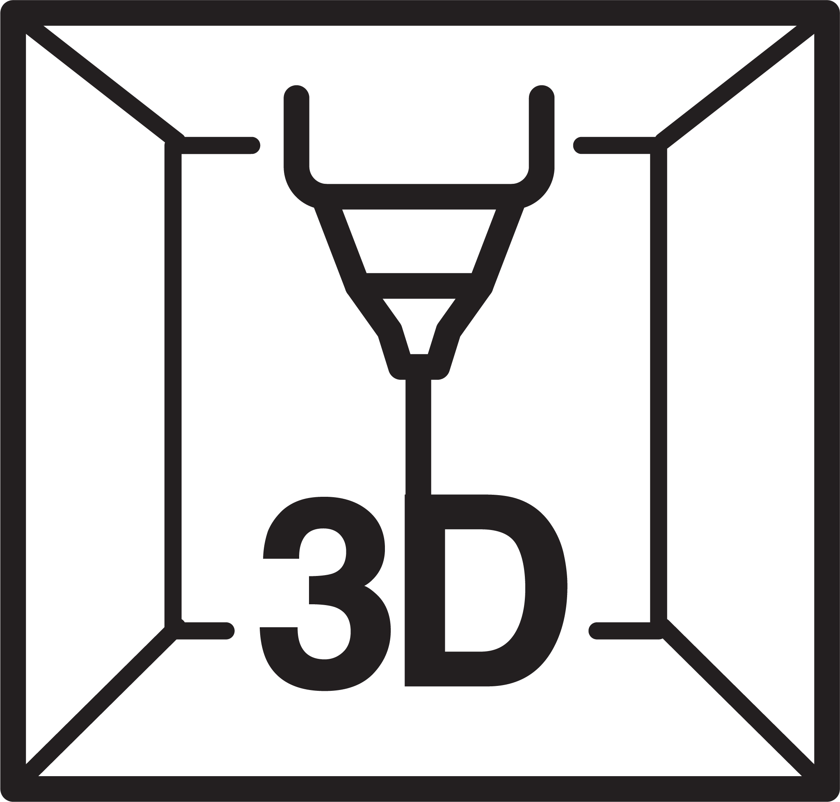
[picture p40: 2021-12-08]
src/images/step_by_step/3d_printing.png

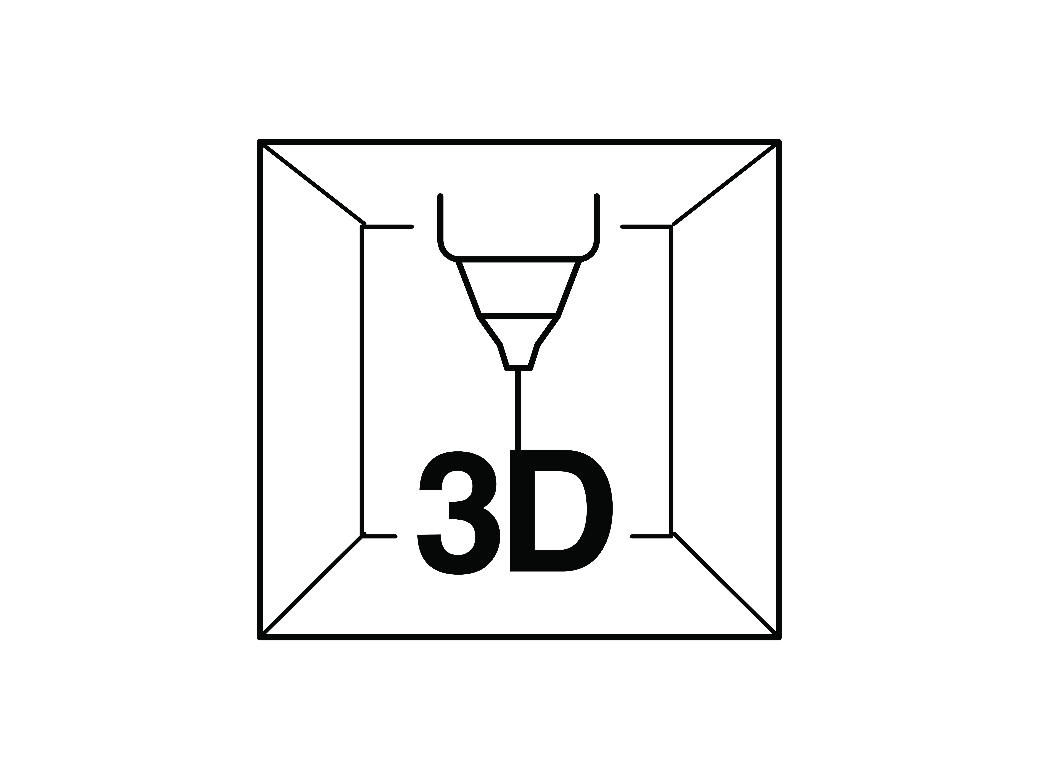
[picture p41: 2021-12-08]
src/images/step_by_step/3d_printing.jpg

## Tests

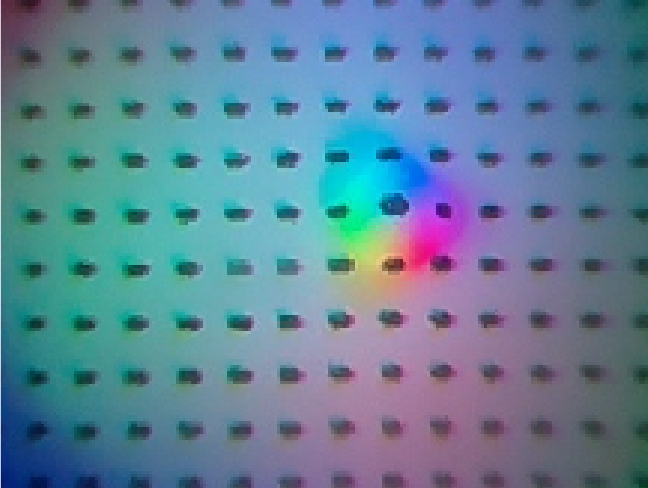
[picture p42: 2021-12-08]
src/images/calibration.png

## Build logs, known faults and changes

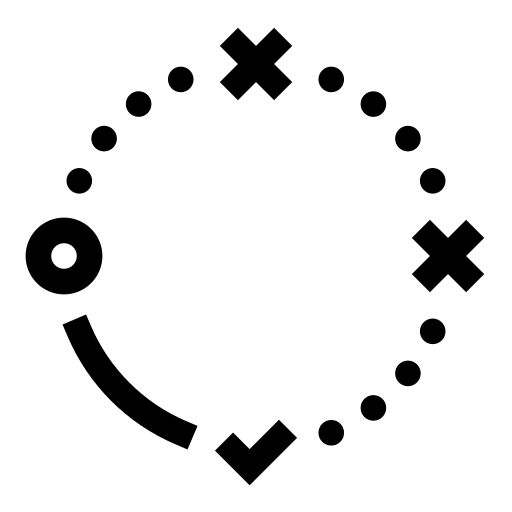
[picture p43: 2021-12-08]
src/images/more_details/known_issues.png

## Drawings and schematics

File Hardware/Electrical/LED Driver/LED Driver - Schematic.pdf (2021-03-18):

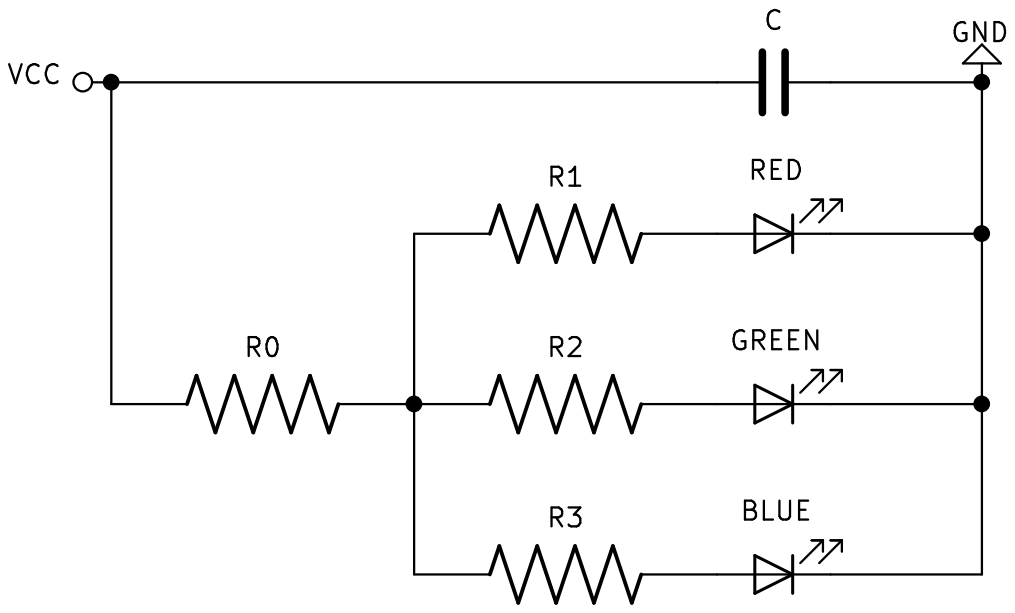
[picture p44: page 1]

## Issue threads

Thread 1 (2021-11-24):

SMD Blue LEDs no longer available

ResiduaLiu, 2021-11-24:
Hi,
It seems that the blue LED is obsolete now. I am wondering if there is any replacement for that?

themcubelab, 2021-12-03:
Yes unfortunately due to COVID supply chain issues it seems the production has stopped. You may be able to use an alternative LED that is a PLCC2 Package Blue LED with a 60 degree vieiwing angle. Here is a [link](https://www.globalsources.com/si/AS/Shenzhen-Best/6008840253093/pdtl/Dome-Blue-LED/1170191189.htm) to one that I found. If you do use this option you will likely need to change the resistance of the blue channel on the pcb.

Closed 2021-12-08.
